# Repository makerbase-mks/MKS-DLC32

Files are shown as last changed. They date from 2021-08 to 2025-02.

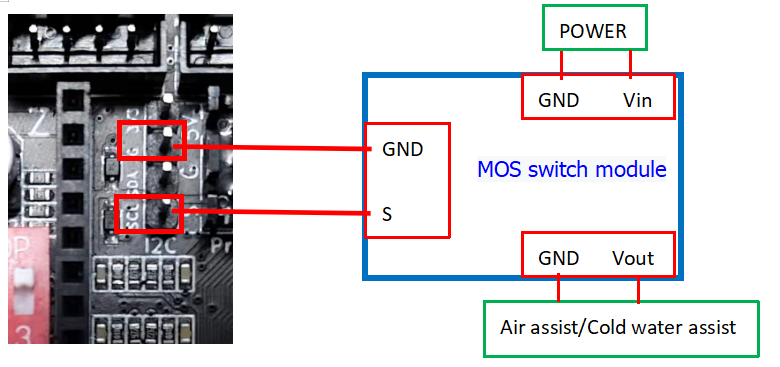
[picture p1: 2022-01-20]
MKS-DLC32-main/images/Hardware Wiring1.png

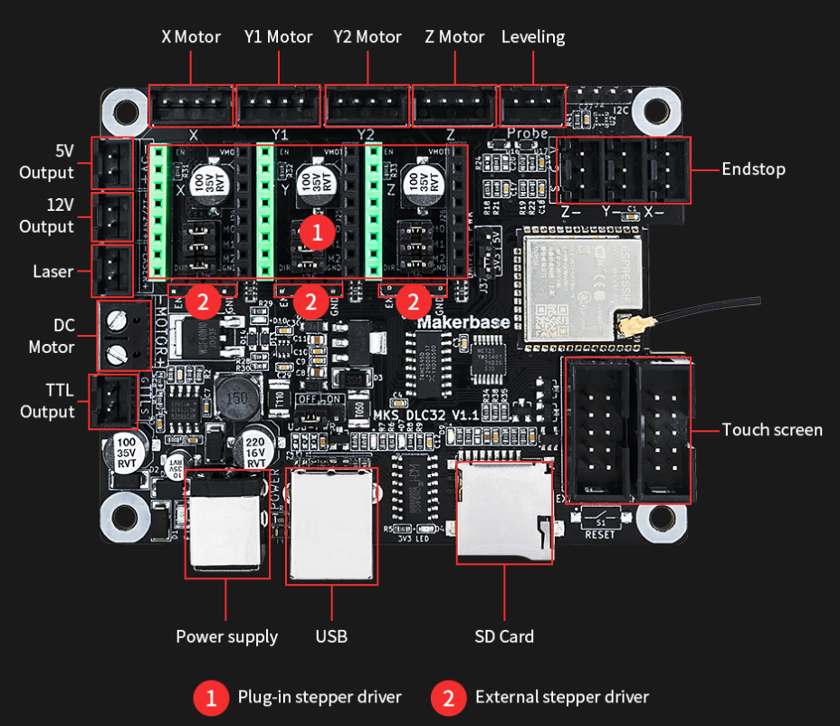
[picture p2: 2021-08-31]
MKS-DLC32-main/images/interface.png

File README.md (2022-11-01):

# MKS-DLC32
MKS DLC32 motherboard kit, which is an offline engraving master control kit developed for desktop engraving machines. The hardware is equipped with a 32-bit high-speed ESP32 module, integrated WIFI function, and directly drives a 3.5-inch touch color screen; it can realize fast engraving and WEB web pages. Control, mobile phone APP control and other functions.  
The mounting holes and board size of MKS DLC32 are compatible with MKS DLC, and the it can also be used with the [LaserGRBL](https://lasergrbl.com) and [LightBurn](https://lightburnsoftware.com) PC software.  
main   

## Related tutorials and Notice
Product introduce video: https://www.youtube.com/watch?v=U_OzlMxwms8&t=6s  
Basic usage for laser engraving machine: https://www.youtube.com/watch?v=MKRBYVbxJmw&t=139s  

# HARDWARE Wiring 
For detailed wiring method, please refer to: https://github.com/makerbase-mks/MKS-DLC32/blob/main/doc/DLC32%20wiring%20manual.pdf

# Compare between MKS DLC and MKS DLC32
| ITEMS | MKS DLC | MKS DLC32 |
| --- | --- | --- |
| MCU | ATMEGA328P ( 8bits) | ESP32-WROOM-32U（ 32bits）  |
| MCU Freq. | 20MHz | 240MHz |
| FLASH | 32KBytes | 8192KBytes |
| RAM | 32KBytes | 520KBytes |
| Power Input | DC 12v/24v | DC12v/24v |
| Laser Speed | <=3000mm/min | <=8000mm/min |
| PC engraving | Support | Support |
| Offline Mode | Not Support | Support |
| LCD | Not Support | Support，3.5 inch Touch TFT |
| WiFi On Board | Not Support | Support |
| Web Control | Not Support | Support |
| Mobile APP Control | Not Support | Support |
| LaserGRBL | Support | Support |
| LightBurn | Support | Support |

# FIRMWARE
Refer to the wiki:https://github.com/makerbase-mks/MKS-DLC32/wiki/Firmware  
Source: https://github.com/makerbase-mks/MKS-DLC32-FIRMWARE  

# Mobile App
Refer to the wiki:https://github.com/makerbase-mks/MKS-DLC32/wiki/Mobile-App

# Wiki
https://github.com/makerbase-mks/MKS-DLC32/wiki

# Purchase link
Aliexpress: https://www.aliexpress.com/item/1005003183498253.html?spm=a2g0o.store_pc_home.productList_8356958.pic_0

## Note
- Thank you for using MKS products. If you have any questions during use, please contact us in time and we will work with you to solve it.
- For more product dynamic information and tutorial materials, you can always follow MKS's Facebook/Twitter/Discord/Reddit/Youtube and Github. Thank you!
- MKS Github: https://github.com/makerbase-mks  
- MKS Facebook: https://www.facebook.com/Makerbase.mks/  
- MKS Twitter: https://twitter.com/home?lang=en  
- MKS Discord: https://discord.gg/4uar57NEyU
- MKS Reddit: https://www.reddit.com/user/MAKERBASE-TEAM/ 

mks_link

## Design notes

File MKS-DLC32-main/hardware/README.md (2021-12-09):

# MKS-DLC32 Hardware
- V2.1_003
  - MKS DLC32 V2.1_003 TOP.pdf
  - MKS DLC32 V2.1_003 BOTTOM.pdf
  - MKS DLC32 V2.1_003 PIN.pdf
  - MKS DLC32 V2.1_003 SCH.pdf
  - MKS DLC32 V2.1_003 SIZE.pdf
  
  change log
  - From V2.1_002 version
    - Add the driver slot silk screen, and the endstops silk screen is on the motherboard BOTTOM
	- V2.1_002 change to V2.1_003

- V2.1_002
  - MKS DLC32 V2.1_002 TOP.pdf
  - MKS DLC32 V2.1_002 BOTTOM.pdf
  - MKS DLC32 V2.1_002 PIN.pdf
  - MKS DLC32 V2.1_002 SCH.pdf
  - MKS DLC32 V2.1_002 SIZE.pdf
  
  change log
  - From V2.1_001 version
    - The direction of J18 buckle is 180 degrees, the line sequence remains unchanged 
	- V2.1_001 change to V2.1_002
  
- V2.1_001
  - MKS DLC32 V2.1_001 TOP.pdf
  - MKS DLC32 V2.1_001 BOTTOM.pdf
  - MKS DLC32 V2.1_001 PIN.pdf
  - MKS DLC32 V2.1_001 SCH.pdf
  - MKS DLC32 V2.1_001 SIZE.pdf
  
  change log
  - From V2.0_001 version
    - Mounting hole adjustment 
	- PCB is black immersion gold 
	- V2.0_001 change to V2.1_001

- V2.0_001
  - MKS DLC32 V2.0_001 TOP.pdf
  - MKS DLC32 V2.0_001 BOTTOM.pdf
  - MKS DLC32 V2.0_001 PIN.pdf
  - MKS DLC32 V2.0_001 SCH.pdf
  - MKS DLC32 V2.0_001 SIZE.pdf
  
  change log
  - From V1.1_002 version
    - Add power switch package(NC)
	- Fuse use plug-in type
	- Add debug led for wifi
	- Reset botton use XH2.54-2P
    - Optimize the laser and spindle circuit (Increase diode)
	- Add beerper interface XH2.54-2P
	- Optimize the driver circuit (add 6.8k for driver output)
	- Relayout and change board outline
	- Some io function adjustments (IO32 for TTL, IO22 for Probe, IO2 for wifi debug led)
	- Microstep settings using DIP switch 
	- V1.1_002 change to V2.0_001

- V1.1_002
  - MKS DLC32 V1.1_002 TOP.pdf
  - MKS DLC32 V1.1_002 BOTTOM.pdf
  - MKS DLC32 V1.1_002 PIN.pdf
  - MKS DLC32 V1.1_002 SCH.pdf
  - MKS DLC32 V1.1_002 SIZE.pdf
  
  change log
  - From V1.1_001 version
    - Optimize the laser circuit 
	- 001 change to 002

- V1.1_001
  - MKS DLC32 V1.1_001 TOP.pdf
  - MKS DLC32 V1.1_001 BOTTOM.pdf
  - MKS DLC32 V1.1_001 PIN.pdf
  - MKS DLC32 V1.1_001 SCH.pdf
  - MKS DLC32 V1.1_001 SIZE.pdf

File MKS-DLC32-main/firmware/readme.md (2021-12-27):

## List of upload Firmware
There are several compiled firmwares that can be downloaded here:  
[For Laser, normal machine](https://github.com/makerbase-mks/MKS-DLC32/tree/main/firmware/Laser/Normal)  
[For Laser, CoreXY machine](https://github.com/makerbase-mks/MKS-DLC32/tree/main/firmware/Laser/CoreXY)  
[For CNC, normal machine](https://github.com/makerbase-mks/MKS-DLC32/tree/main/firmware/CNC/Normal)(For beta)  
The firmware of MKS DLC32 has been burned with laser normal machine before leaving the factory. 

## Method of upload Firmware

You can either use the "MKS ESP32 Download Tool" or "Flash Download Tools" upload firmware of MKS DLC32.
### MKS ESP32 Download Tool
MKS ESP32 Download Tool is specially developed by MKS to simplify the uploading operation. It is recommended to use. For detailed usage, please refer to:https://github.com/makerbase-mks/MKS-DLC32/blob/main/doc/DLC32%20Firmware%20Programming%20Instructions.pdf

### Flash Download Tools
#### Windows

1. On Windows PC, download the "Flash Download Tools" from https://www.espressif.com/en/support/download/other-tools 
2. Open the "Flash Download Tools", choose "Developer Mode"->ESP32 DowloadTool, and it will open the main menu.
3. Config the Flash Download Tools  
3.1 Choose the firmware(binary file listed above) and fill the address to be 0  
3.2 Config the  spiFlash  
SPI speed: 40MHz  
SPI MODE: DOUT  
Flash Size: 32Mbit  
3.3 Connect MKS DLC32 to PC using the USB line. Choose the COM of the DLC32, if you can’t find the COM, please check if the CH340 driver has been installed on the PC.  
3.4 Choose the baudrate which can be over 115200(The greater the baud rate, the faster the transmission speed, but the greater the chance of transmission errors).  
3.5 Press START and it will start to upload, just wait it to be finished.

微信图片_20210908150315

#### Linux

* Install esptool.py
```
pip install esptool
```

* Provide valid path to port/firmware and burn the ESP32 chip
```
esptool.py --baud 300000 --chip esp32 --port /dev/ttyUSB0 write_flash --flash_mode dio --flash_size detect 0x0 TS35/Laser/Normal/Board_V2.0/V2.0.4_H35_20211123_N.bin
```

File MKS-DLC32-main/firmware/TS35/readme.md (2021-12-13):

# Version description

## E.g：

### V2.0.4_H35_20211108_N

V2.0.4.: Firmware version

H35: Horizontal screen- 3.5Inch

20211108： Modified date （2021-11-08）

N：N for normal machine, C for CoreXY machine

(for DLC V2.x, coreXY): As there is a little difference between DLC V1.x and V2.x boards, so we would explain what board the firmware is suitable for. 
**Please use the correct version, otherwise it may not work.**

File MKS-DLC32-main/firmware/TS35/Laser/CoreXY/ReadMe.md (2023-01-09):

# Update:
## Version description

E.g：

### V2.0.3_H35_20211108_N

V2.0.3.: Firmware version

H35: Horizontal screen- 3.5Inch

20211108： Modified date （2021-11-08）

N：N for normal machine, C for CoreXY machine

(for DLC V2.x, coreXY): As there is a little difference between DLC V1.x and V2.x boards, so we would explain what board the firmware is suitable for. Please use the correct version, otherwise it may not work.

### 2022-12-23

##### Update version: V2.30_H35_2022_1223_C_ZX_001

- Fixed incompatibility between UI buttons and background
- Fixed an issue where WiFi could not be found
- Temporarily cancel automatic WiFi reconnection
- Fixed some other known bugs

### 2022-07-04

##### Update version: V2.10_H35_2022_0704_C_ZX_001

- Add z-axis control on the screen
- Add German, Spanish and Portuguese
- Add a cooling button
- Add the symbol "_" to the keyboard
- Fix some known bugs

## Update:

### 2022-01-05

##### Update version: V2.0.8_H35_20220105_C

- Fixed the problem of "warning text" displayed abnormally in the pop-up window after clicking the positioning during the moving process
- In the Chinese environment, the display of "Continue/Cancel" in the pop-up window of more than 1M side patrol is missing
- Unable to flash configuration file
- Inaccurate screen edge size

### 2021-12-22

##### Update version: V2.0.8_H35_20211222_C

- Fix part of the error display
- Fix language errors
- Optimize wifi function
- WebUI updated

### 2021-12-13

##### Update version: V2.0.7_H35_20211213_C

- Fix language display error
- Join the function of MIST, you can use M7/M9 to control，Connect the control signal pin to the SCL pin of I2C. The control level of SCL is only 0-3.3V, so an external level conversion module is required for control

### 2021-12-07

##### Update version: V2.0.6_H35_20211207_C

- Fix the version number error displayed on Lightburn

### 2021-11-23

**Update version: V2.0.4_H35_20211123_C**

Fix content

- Optimize the time to automatically connect to the wifi  
- Fix the problem that it cannot be moved when $1=255  
- Modify the language switch interface  
- Fixed the problem of searching blank lists when searching on wifi  
- Fixed the problem that the options on the power adjustment interface did not change after triggering the laser automatic protection, and the problem that the value on the main page did not change  
- Fix some pop-up errors

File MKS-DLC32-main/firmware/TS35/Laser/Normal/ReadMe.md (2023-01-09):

# Update:
## Version description

E.g：

### V2.0.3_H35_20211108_N

V2.0.3: Firmware version

H35: Horizontal screen- 3.5Inch

20211108： Modified date （2021-11-08）

N：N for normal machine, C for CoreXY machine

(for DLC V2.x, coreXY): As there is a little difference between DLC V1.x and V2.x boards, so we would explain what board the firmware is suitable for. Please use the correct version, otherwise it may not work.

## Update:

### 2022-12-23

##### Update version: V2.30_H35_2022_1223_N_ZX_001

- Fixed incompatibility between UI buttons and background
- Fixed an issue where WiFi could not be found
- Temporarily cancel automatic WiFi reconnection
- Fixed some other known bugs

### 2022-11-04

##### Update version: V2.20_H35_2022_1101_N_ZX_002

- Change the UI
- Optimize file transfer
- Added WiFi mode switching through the screen
- Fix some known bugs

### 2022-06-29

##### Update version: V2.10_H35_2022_0621_N_ZX_001

- Add z-axis control on the screen
- Add German, Spanish and Portuguese
- Add a cooling button
- Add the symbol "_" to the keyboard
- Fix some known bugs

### 2022-01-05

##### Update version: V2.0.8_H35_20220105_N

- Fixed the problem of "warning text" displayed abnormally in the pop-up window after clicking the positioning during the moving process
- In the Chinese environment, the display of "Continue/Cancel" in the pop-up window of more than 1M side patrol is missing
- Unable to flash configuration file
- Inaccurate screen edge size

### 2021-12-22

##### Update version: V2.0.8_H35_20211222_N

- Fix part of the error display
- Fix language errors
- Optimize wifi function
- WebUI updated

### 2021-12-13

**Update version: V2.0.7_H35_20211213_N**

- Fix language display error
- Join the function of MIST, you can use M7/M9 to control，Connect the control signal pin to the SCL pin of I2C. The control level of SCL is only 0-3.3V, so an external level conversion module is required for control

### 2021-12-07

**Update version: V2.0.6_H35_20211207_N**

- Fix the version number error displayed on Lightburn

### 2021-11-23

**Update version: V2.0.4_H35_20211123_N**

Fix content

- Optimize the time to automatically connect to the wifi  
- Fix the problem that it cannot be moved when $1=255  
- Modify the language switch interface  
- Fixed the problem of searching blank lists when searching on wifi  
- Fixed the problem that the options on the power adjustment interface did not change after triggering the laser automatic protection, and the problem that the value on the main page did not change  
- Fix some pop-up errors

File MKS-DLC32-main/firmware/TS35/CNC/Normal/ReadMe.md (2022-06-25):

# Update:
### 2022-06-25

##### Update version: V2.1.0_H35_20220526_02_N_CNC

- Add the thickness setting of the short-circuit block (set the value of $46)
- Add hard reset button and sound control switch button on the screen
- Add symbol "_" to keyboard
- Fix some known bugs

### 2022-05-11

##### Update version: V2.1.0_H35_20220510_N_CNC_001

- Add on-screen knife buttons
- Add button sound and Chinese environment
- Disable the automatic return to zero after the engraving is complete
- Adjust the WEB interface
- Fix some known bugs

### 2022-01-05

##### Update version: V2.0.8_H35_20211222_N_CNC

- Fix the problem that the configuration file cannot be recognized
- Fix the WiFi name is not displayed after automatically connecting to WiFi
- Cancel M7, retain M8, release Z limit function, you can configure whether Z return to zero is required through instructions

### 2021-12-22

##### Update version: V2.0.8_H35_20211222_N_CNC

- Fix part of the error display
- Fix language errors
- Optimize wifi function
- WebUI updated
- Fix the problem of returning to zero error

## 2021.12.13

##### Update version: V2.0.7_H35_20211213_N_CNC

- Fixed incorrect display of some languages
- Add FlOOD control function, use M8 control, M9 disable，Connect the control signal pin to the SCL pin of I2C. The control level of SCL is only 0-3.3V, so an external level conversion module is required for control

## 2021.12.07

##### Update version: V2.0.6_H35_20211207_N_CNC

- Fixed the incorrect version number displayed when using Lightburn
- Repair abnormal speed during engraving
- Join wifi automatic connection
- Add the function of Probe, you can use external probe

## 2021.12.06

**Update version: V2.0.4_H35_20211206_N_CNC.bin**

 - Repair the power display is not correct after returning to zero
 - Join wifi to automatically reconnect
 - Fix the problem of garbled characters in the card reader

## 2021.11.23
**Update version: V1.21_H35_20211009_N_CNC.bin**

 - Fix the problem that $1=255 cannot be locked 
 - Fix the problem that after some pop-up windows appear, they can't pop up in the follow-up 
 - Fix the problem of Z zero return error 
 - Fix the problem that the default value is not restored when re-sculpting after adjusting FeedOverride/SpindleSpeedOverride during engraving

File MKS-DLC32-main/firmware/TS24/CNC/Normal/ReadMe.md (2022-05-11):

# Update:
## Version description

E.g：

### V2.0.3_H35_20211108_N

V2.0.3: Firmware version

H35: Horizontal screen- 3.5Inch

20211108： Modified date （2021-11-08）

N：N for normal machine, C for CoreXY machine

(for DLC V2.x, coreXY): As there is a little difference between DLC V1.x and V2.x boards, so we would explain what board the firmware is suitable for. Please use the correct version, otherwise it may not work.

## Update:

### 2022-05-11

##### Update version: V2.1.0_H24_20220511_01_N_CNC

- Add on-screen knife buttons
- Add button sound and Chinese environment
- Disable the automatic return to zero after the engraving is complete
- Adjust the WEB interface
- Fix some known bugs

### 2022-01-08

**Update version: V2.0.8_H24_20220108_N_CNC**

- Change the direction of the Y-axis of the control interface to make it consistent with the direction of LASERGRBL
- On the keyboard, use "AB" and "ab" to replace spaces when switching between uppercase and lowercase

### 2021-12-23

**Update version: V2.0.8_H24_20211223_N_CNC**

- Fix some language description errors
- Adjust the position of the X and Y icons
- Fix the problem of incorrect display of the version number on the web

### 2021-12-22

**Update version: V2.0.8_H24_20211222_N_CNC**

- Fix language errors
- Update webUI
- Fix the problem that Probe does not work
- Optimize wifi function

### 2021-12-14

**Update version: V2.0.7_H24_20211214_N_CNC**

- Fix language display error
- Add FlOOD control function, use M8 control, M9 disable，Connect the control signal pin to the SCL pin of I2C. The control level of SCL is only 0-3.3V, so an external level conversion module is required for control
- Add the function of Probe, you can use external probe

### 2021-12-09

**Update version: V2.0.6_H24_20211209_N_CNC**

- Fix the version number error displayed on Lightburn

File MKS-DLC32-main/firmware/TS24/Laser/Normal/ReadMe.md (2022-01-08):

# Update:
## Version description

E.g：

### V2.0.3_H35_20211108_N

V2.0.3: Firmware version

H35: Horizontal screen- 3.5Inch

20211108： Modified date （2021-11-08）

N：N for normal machine, C for CoreXY machine

(for DLC V2.x, coreXY): As there is a little difference between DLC V1.x and V2.x boards, so we would explain what board the firmware is suitable for. Please use the correct version, otherwise it may not work.

## Update:

### 2022-01-08

**Update version: V2.0.8_H24_20220107_N**

- Change the direction of the Y-axis of the control interface to make it consistent with the direction of LASERGRBL
- On the keyboard, use "AB" and "ab" to replace spaces when switching between uppercase and lowercase

### 2021-12-23

**Update version: V2.0.8_H24_20211223_N**

- Adjust X, Y icon position

### 2021-12-22

**Update version: V2.0.8_H24_20211222_N**

- Fix language errors
- Update webUI
- Optimize wifi function

### 2021-12-14

**Update version: V2.0.7_H24_20211214_N**

- Fix language display error
- Join the function of MISP, you can use M7/M9 to control，Connect the control signal pin to the SCL pin of I2C. The control level of SCL is only 0-3.3V, so an external level conversion module is required for control

### 2021-12-09

**Update version: V2.0.6_H24_20211209_N**

- Fix the version number error displayed on Lightburn

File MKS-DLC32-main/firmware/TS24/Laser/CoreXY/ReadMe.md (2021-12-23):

# Update:
## Version description

E.g：

### V2.0.3_H35_20211108_N

V2.0.3: Firmware version

H35: Horizontal screen- 3.5Inch

20211108： Modified date （2021-11-08）

N：N for normal machine, C for CoreXY machine

(for DLC V2.x, coreXY): As there is a little difference between DLC V1.x and V2.x boards, so we would explain what board the firmware is suitable for. Please use the correct version, otherwise it may not work.

## Update:

### 2021-12-23

**Update version: V2.0.8_H24_20211223_C**

- Adjust X, Y icon position

**Update version: V2.0.8_H24_20211222_C**

- Fix language errors
- Update webUI
- Optimize wifi function

### 2021-12-14

**Update version: V2.0.7_H24_20211214_C**

- Fix language display error
- Join the function of MISP, you can use M7/M9 to control，Connect the control signal pin to the SCL pin of I2C. The control level of SCL is only 0-3.3V, so an external level conversion module is required for control

### 2021-12-09

**Update version: V2.0.6_H24_20211209_C**

- Fix the version number error displayed on Lightburn

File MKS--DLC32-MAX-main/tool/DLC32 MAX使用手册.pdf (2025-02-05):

# MKS DLC32 MAX 主板使用说明

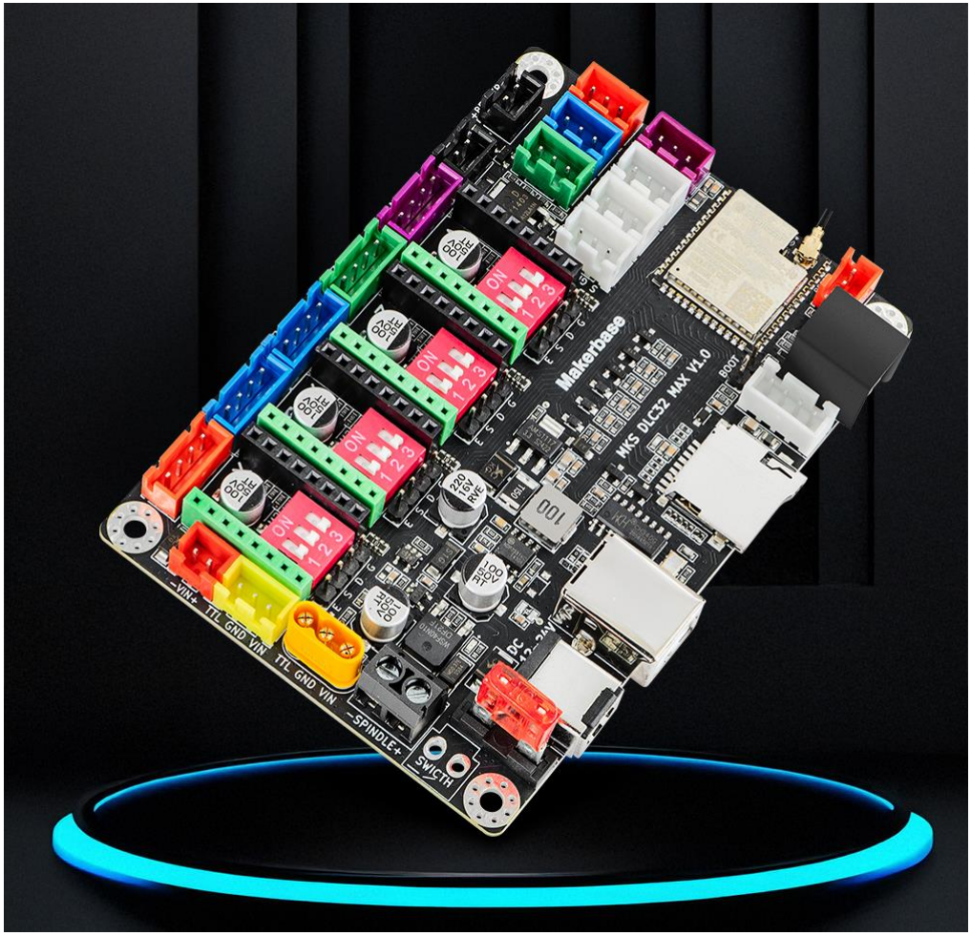
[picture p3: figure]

简介

MKS DLC32 MAX 激光雕刻控制板由创客基地(Makerbase)倾力打造,是一款集高性能强扩展性与智能操

控于一体的雕刻控制解决方案。搭载 ESP32-S3 系列芯片，同时支持 CNC 与激光雕刻，可支持 CNC 的 A

轴，激光雕刻机最大可达 60W 激光头雕刻功率与 30000mm/min 速度，满足高效创作。

可以兼容插拔式驱动扩展性强，如可接 TMC2209 超静音驱动方案和 TB67S109 大电流驱动模块，另外

还可以连接外部驱动。

安全方面，可以配备开盖保护、火焰检测等智能安全功能，为用户创作保驾护航。

可以无需长时间连接电脑,支持手机 APP 与 Web 局域网远程控制,让操作更加自由便捷,不论是激光雕

刻还是 CNC 应用，MKS DLC32 MAX 都是解锁创意无限的理想选择!

本文档可作为初次使用 MKS DLC32 主板参考，文档将会从以下几部分进行说明：

固件的下载与更新，硬件连接说明，Wifi 连接说明及远程控制说明，主板参数设置

，主板常见问题及其解决办法。

目录

一． 固件的下载与更新---------------------------------------------------------------------------------------------------------------------4

1. 固件与烧录软件的下载 -------------------------------------------------------------------------------------------------------------4

1.1 固件的选择与下载 -------------------------------------------------------------------------------------------------------------4

1.2 烧录软件与 USB 驱动软件安装---------------------------------------------------------------------------------------------4

2. 烧录软件的安装于说明与固件烧录 ---------------------------------------------------------------------------------------------5

2.1 软件安装与连接-----------------------------------------------------------------------------------------------------------------5

2.2 软件介绍与固件烧录----------------------------------------------------------------------------------------------------------7

二． 主板硬件连接及接口说明-----------------------------------------------------------------------------------------------------------9

1. 主板接口图及安装尺寸-------------------------------------------------------------------------------------------------------------9
2. DLC32 主板接口说明---------------------------------------------------------------------------------------------------------------- 10

2.1 电源输入部分------------------------------------------------------------------------------------------------------------------ 10

2.2 电机驱动部分------------------------------------------------------------------------------------------------------------------ 11

2.3 激光头接法--------------------------------------------------------------------------------------------------------------------- 13

2.4 CNC 主轴接法------------------------------------------------------------------------------------------------------------------ 15

2.5 限位开关------------------------------------------------------------------------------------------------------------------------ 16

2.6 PROBE（对刀）、安全接口------------------------------------------------------------------------------------------------- 17

2.8 蜂鸣器、空气辅助接口---------------------------------------------------------------------------------------------------- 17

2.9 急停开关接口：--------------------------------------------------------------------------------------------------------------- 18

2.10 屏幕、手柄接口------------------------------------------------------------------------------------------------------------- 18

2.11 TF 卡、PC 接口 --------------------------------------------------------------------------------------------------------------- 19

三 . 主板参数设置-------------------------------------------------------------------------------------------------------------------------- 19

四．常见支持指令--------------------------------------------------------------------------------------------------------------------------- 22

五．常见报错说明--------------------------------------------------------------------------------------------------------------------------- 23

六．主板常见问题及其解决办法 ------------------------------------------------------------------------------------------------------- 24

七 . 技术支持及保证----------------------------------------------------------------------------------------------------------------------- 25

## 一． 固件的下载与更新

操作流程如下：

- 固件与烧录软件的下载
- 烧录软件的安装于说明与固件烧录

### 1. 固件与烧录软件的下载

MKS 官方的 Github 进行下载：https://github.com/makerbase-mks/MKS-DLC32

### 1.1 固件的选择与下载

打开以上链接后，选择“MKS--DLC32-MAX-main”这栏打开，然后下里面的固件即可，如下图所示：

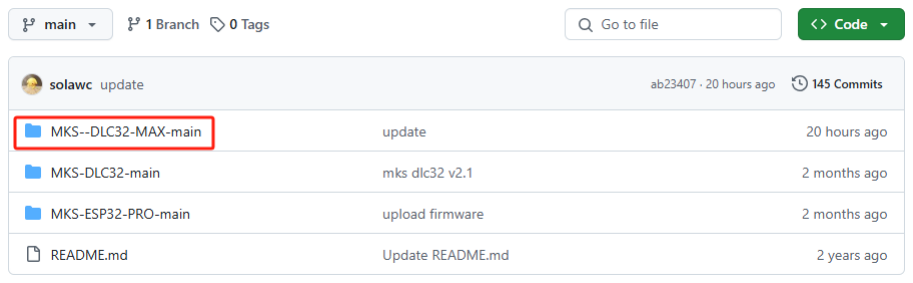
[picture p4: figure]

### 1.2 烧录软件与 USB 驱动软件安装

下载链接

https://github.com/makerbase-mks/MKS-DLC32/tree/main/MKS--DLC32-MAX-main/tool

MKS LaerTool 烧录软件和 CH340 驱动安装文件下载页面最新版本即可。

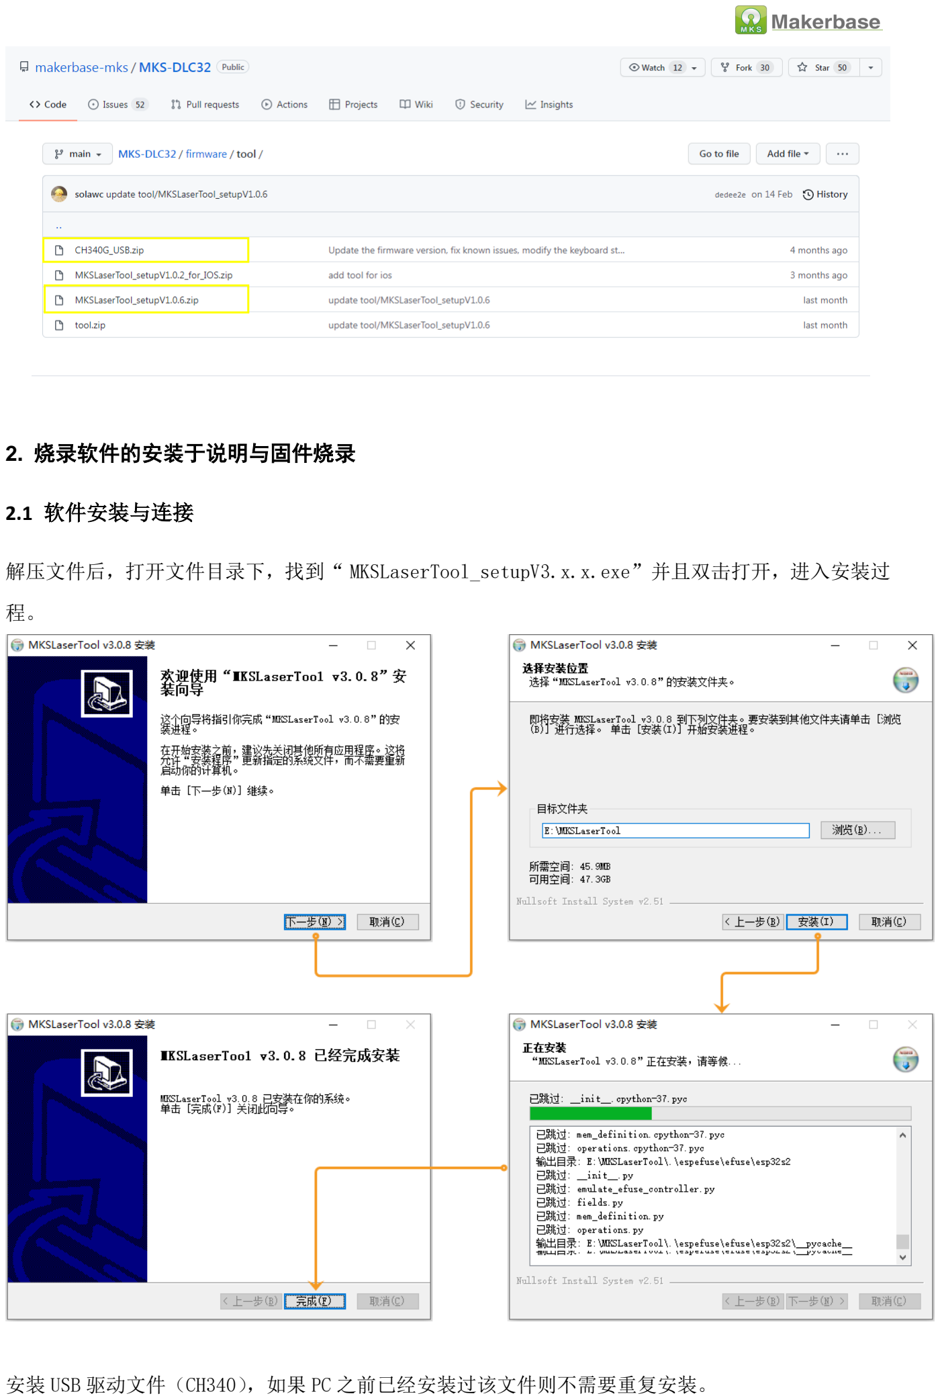
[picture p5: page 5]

### 2. 烧录软件的安装于说明与固件烧录

### 2.1 软件安装与连接

解压文件后，打开文件目录下，找到“ MKSLaserTool_setupV3.x.x.exe”并且双击打开，进入安装过

程。

安装 USB 驱动文件（CH340），如果 PC 之前已经安装过该文件则不需要重复安装。

安装完成之后，可将 MKS DLC32 主板通过 USB 线连接至 PC，在 PC 设备管理中，查看主板是否有被分

配相应的 COM。正常分配则主板已连接上 PC,如果没有显示的话，请重新检查软件的安装，和硬件的连

接是否存在问题。

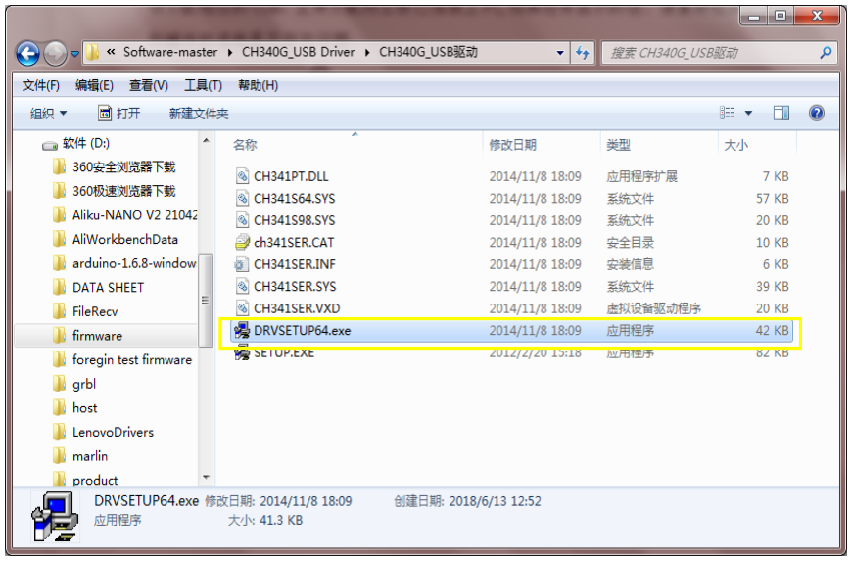
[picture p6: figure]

主板在连接 USB 到 PC 时，同时需要连接 12-24v 进行供电，如果未连接 12-24v 供电，主板将无法别识

别。

如下图，为连接后，com 正确识别。

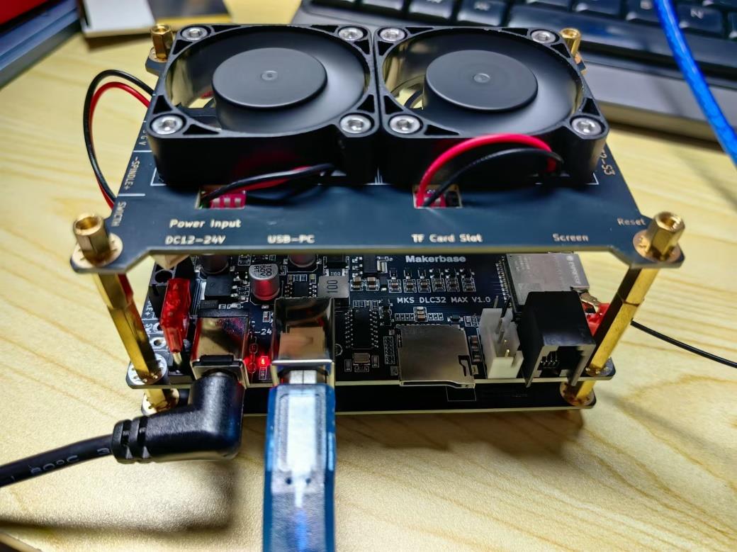
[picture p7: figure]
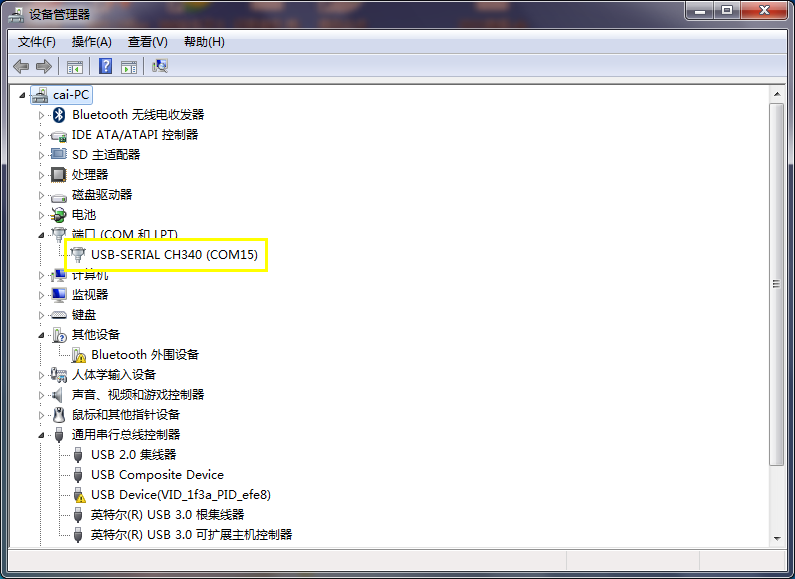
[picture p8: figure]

### 2.2 软件介绍与固件烧录

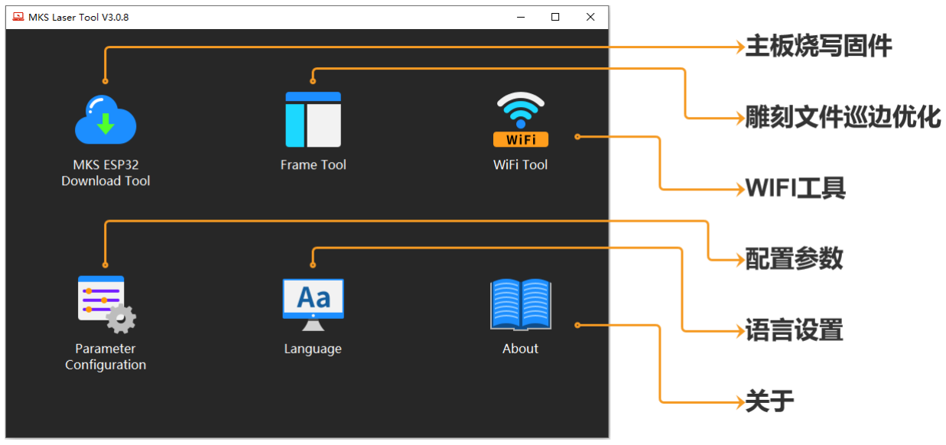
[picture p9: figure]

点击“MKS ESP32 Download Tool”，进入烧写界面

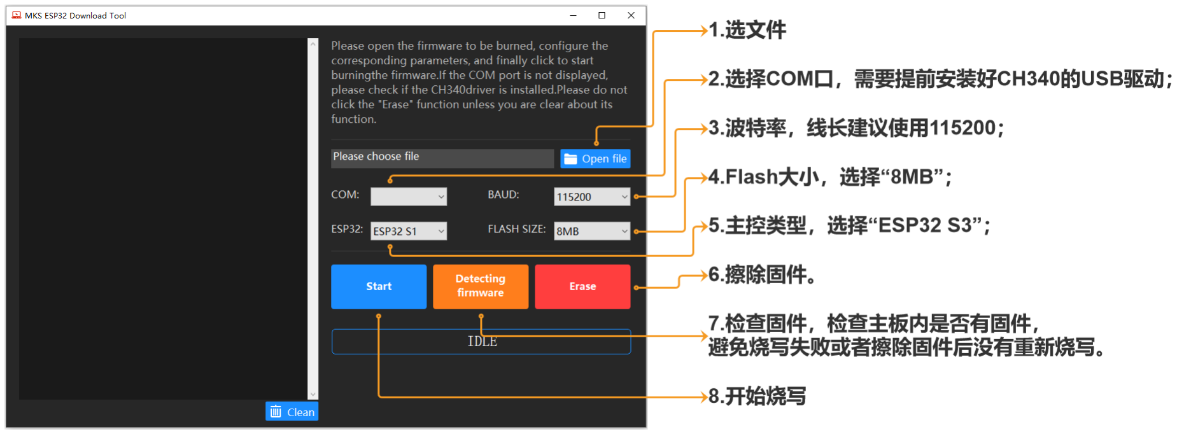
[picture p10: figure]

烧录文件为从 github 下载，符合机器情况的 bin 文件。

COM:可在设备管理器中，查看到具体的 COM 序号，按照实际情况进行设置。

BAUD：波特率一般建议选择 115200。

Flash 大小：这个需要选择 8MB 的。

主控类型：选择 ESP32 S3。

烧写步骤：点击烧写按键。如果出现烧写失败时，先点击擦除，然后再点击烧写，并且将波特率数值

降低。

完成设置之后，点击开始，等待烧录完成即可。

## 二． 主板硬件连接及接口说明

1. 主板接口图及安装尺寸

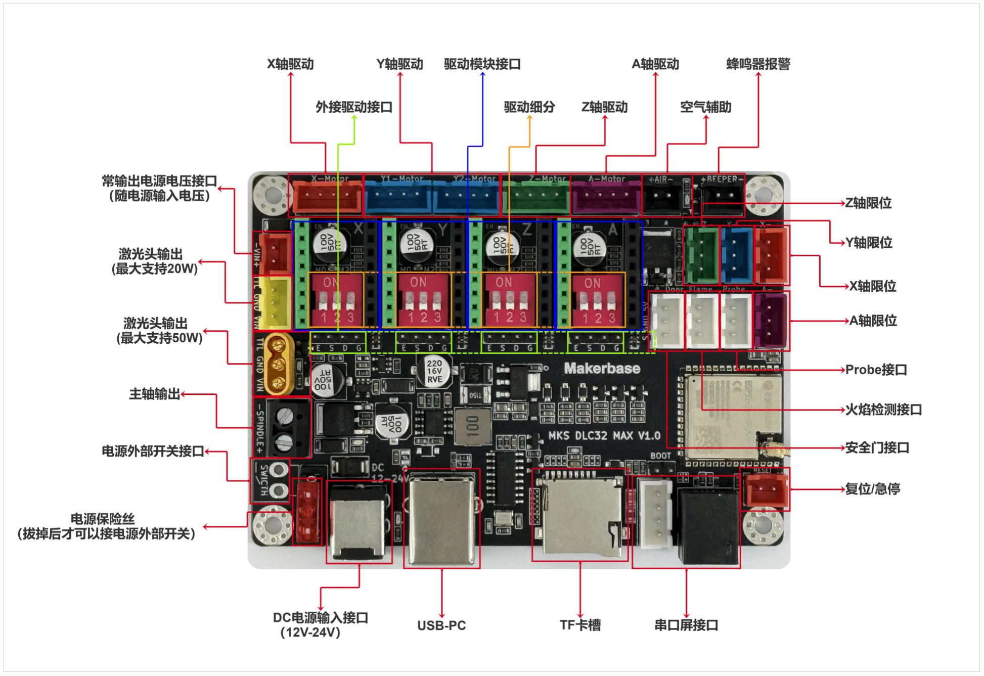
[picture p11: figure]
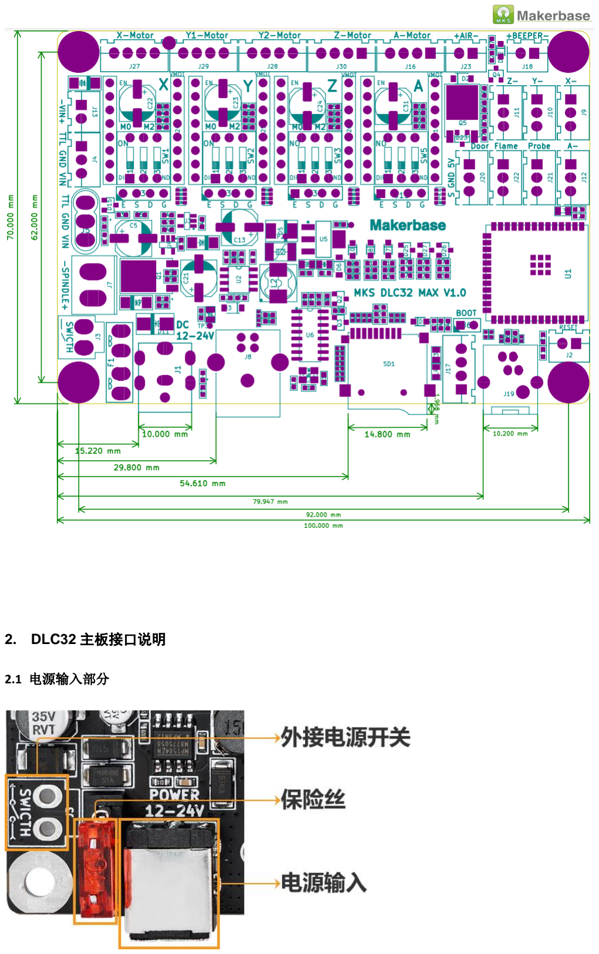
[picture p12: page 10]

### 2. DLC32 主板接口说明

### 2.1 电源输入部分

电源输入：该接口可接 12V 或者 24V 电源，最大承受电流 5A，电源输入端子为“DC-007B-2.1mm”接

口。

保险丝：10A 保险丝，如需外接开关控制电源，需要拔掉保险丝才可以。

外接电源开关：可以用来外接开关来控制电源，但需要拔掉保险丝。注意：这个接口不是电源输入接

口，切记不能接电源。

### 2.2 电机驱动部分

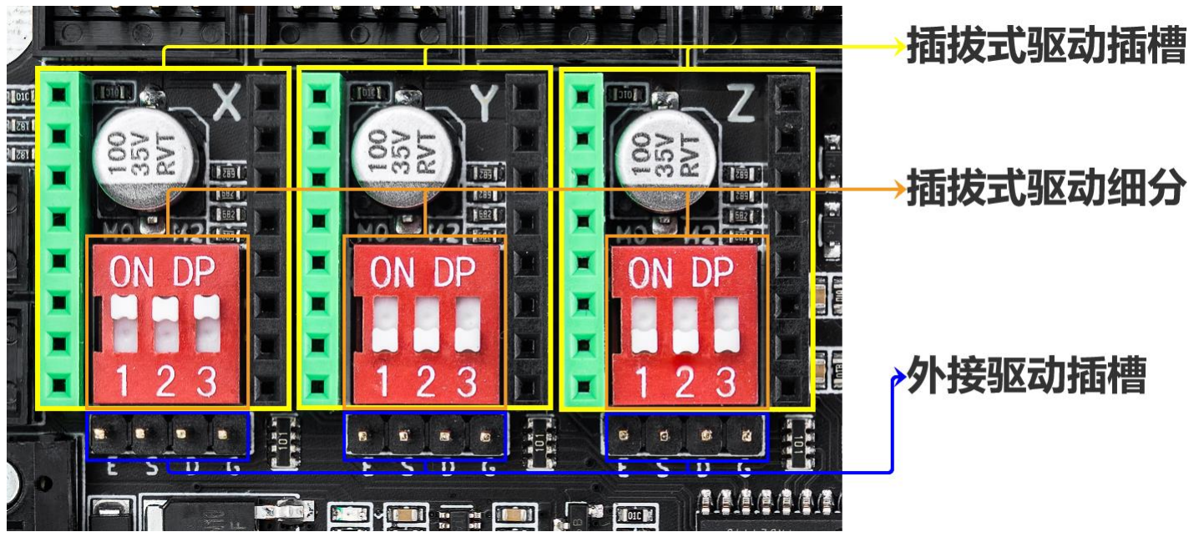
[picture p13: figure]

2.2.1 接口示意图

插拔式驱动插槽 PIN | 插拔式驱动细分设置开关

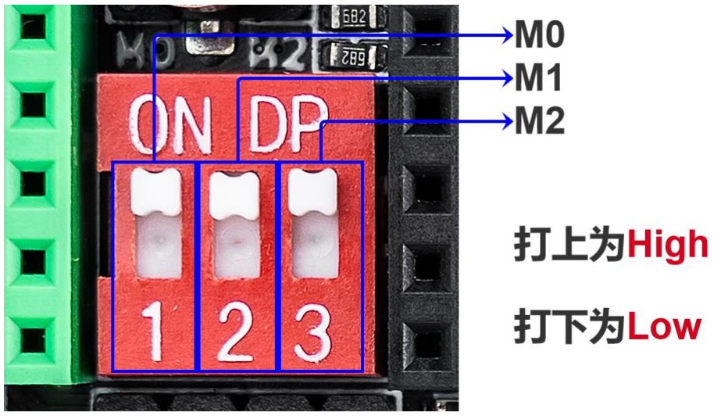
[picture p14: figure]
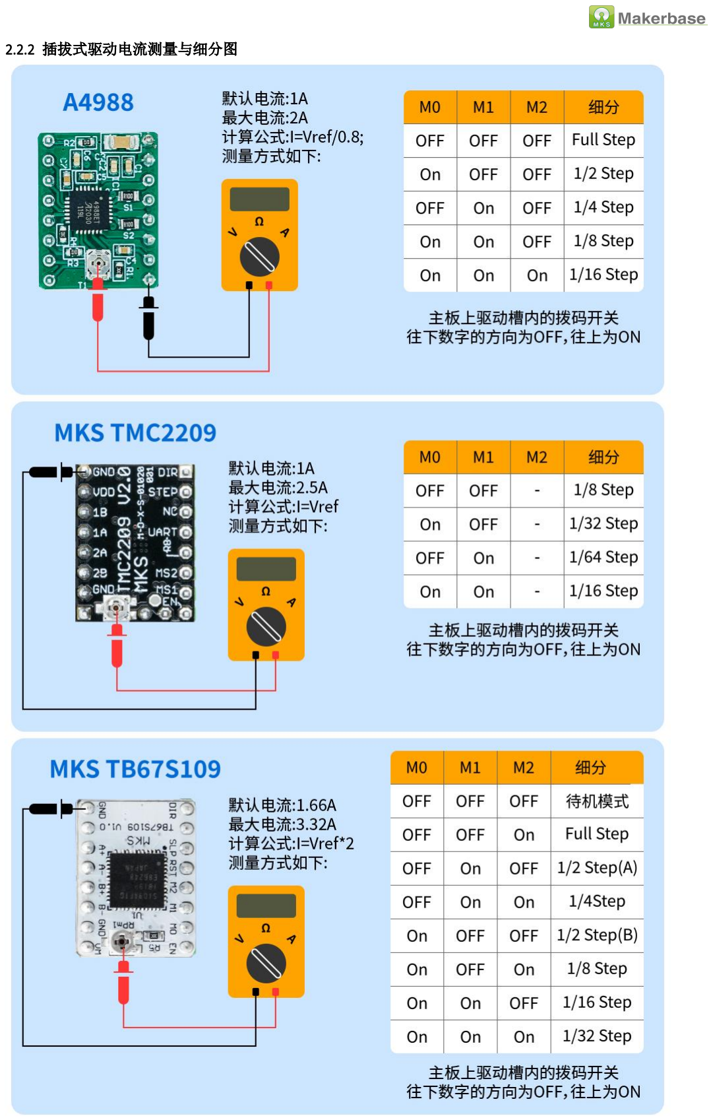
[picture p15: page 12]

2.2.2 插拔式驱动电流测量与细分图

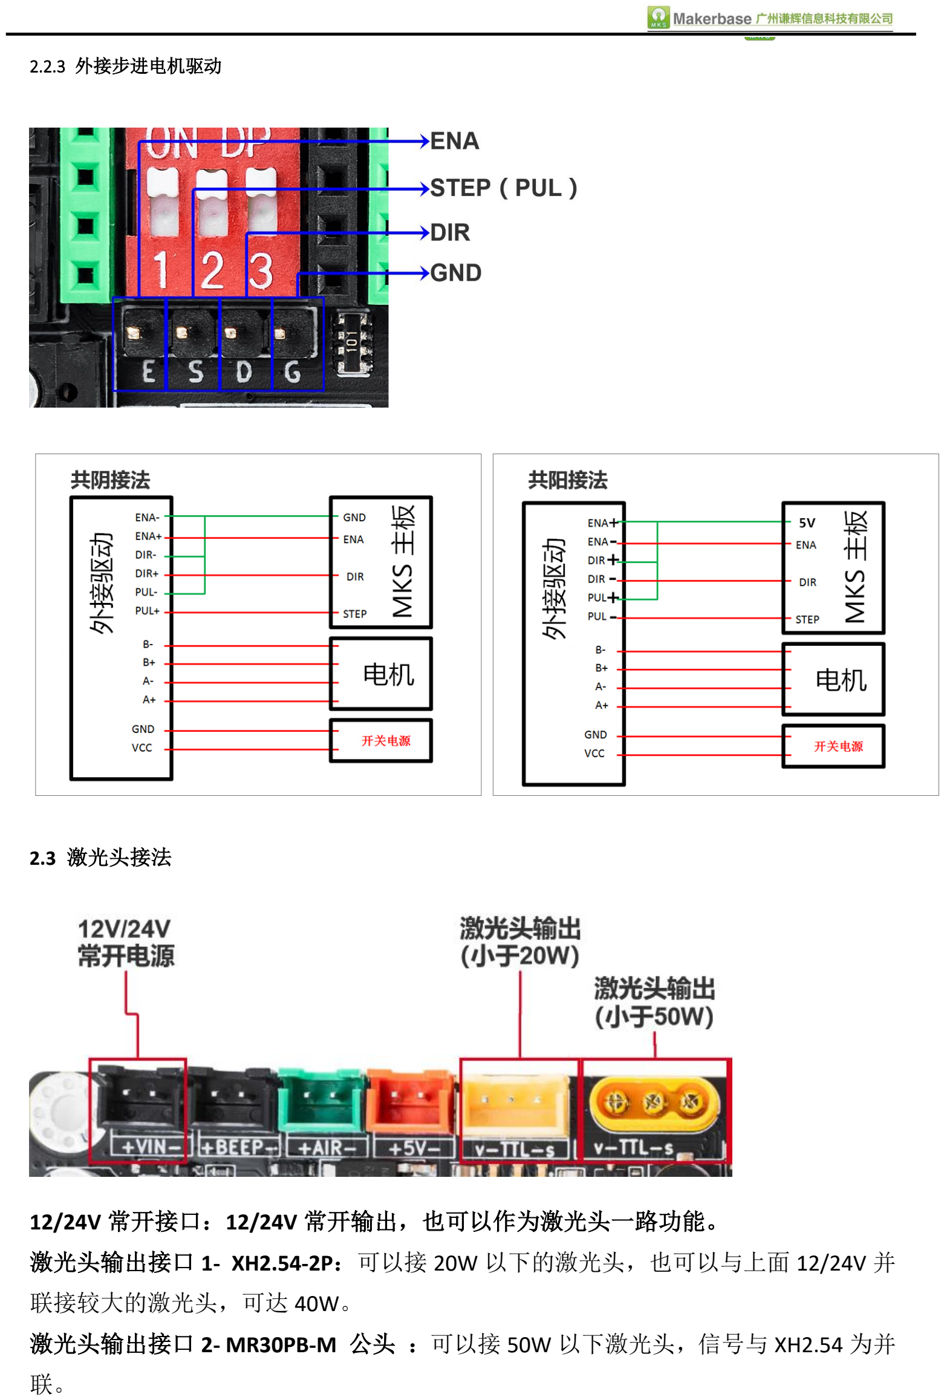
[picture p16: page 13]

2.2.3 外接步进电机驱动

### 2.3 激光头接法

### 12/24V 常开接口：12/24V 常开输出，也可以作为激光头一路功能。

### 激光头输出接口 1- XH2.54-2P：可以接 20W 以下的激光头，也可以与上面 12/24V 并

### 联接较大的激光头，可达 40W。

### 激光头输出接口 2- MR30PB-M 公头 ：可以接 50W 以下激光头，信号与 XH2.54 为并

联。

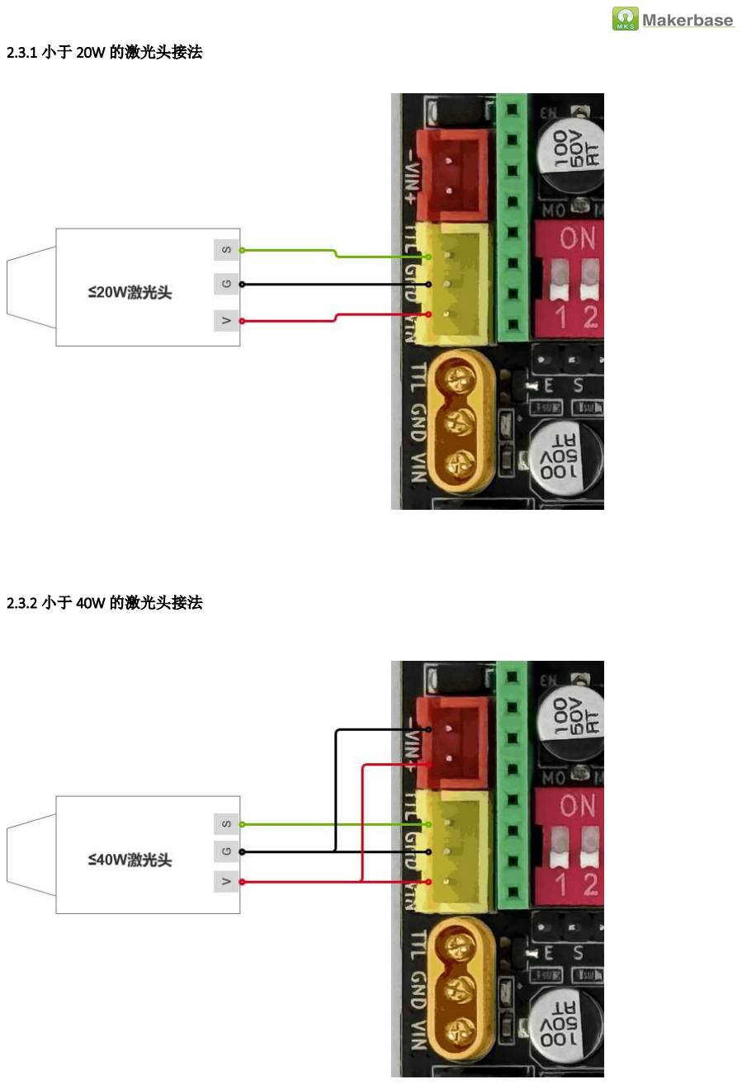
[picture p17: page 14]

2.3.1 小于 20W 的激光头接法

2.3.2 小于 40W 的激光头接法

2.3.3 小于 50W 的激光头接法

2.4 CNC 主轴接法

SPINDLE 接口：用于接主轴（直流电机），这个口为输出口，输出电压为 0-12V 或 0-24V，最大电压取

决于输入电源的电压。如电源的输入电压为 24V，则 SPINDLE 接口输出最大电压为 24V。目前主轴电机

支持最大功率为：12V 时最大支持 10W，24V 时最大支持 20W。

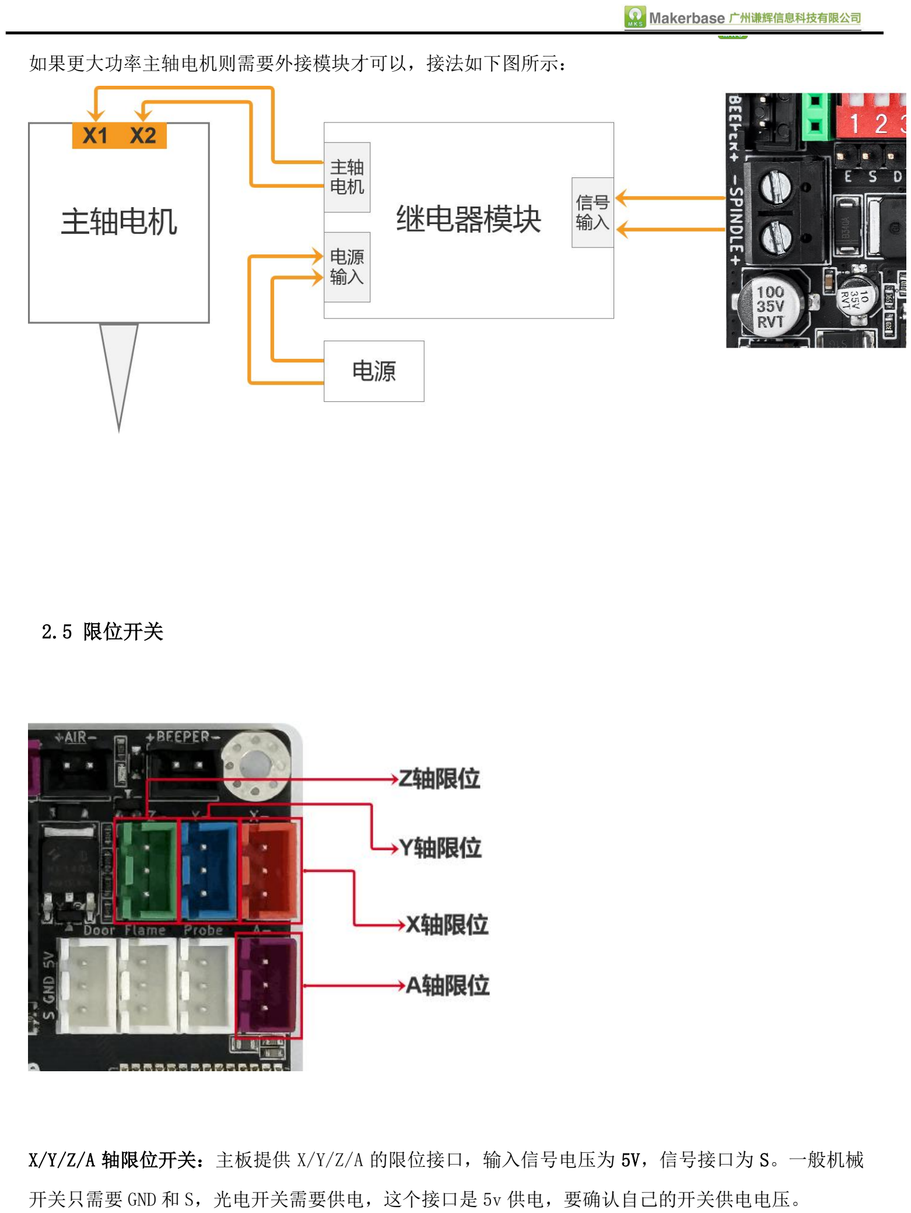
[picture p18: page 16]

如果更大功率主轴电机则需要外接模块才可以，接法如下图所示：

2.5 限位开关

X/Y/Z/A 轴限位开关：主板提供 X/Y/Z/A 的限位接口，输入信号电压为 5V，信号接口为 S。一般机械

开关只需要 GND 和 S，光电开关需要供电，这个接口是 5v 供电，要确认自己的开关供电电压。

2.6 PROBE（对刀）、安全接口

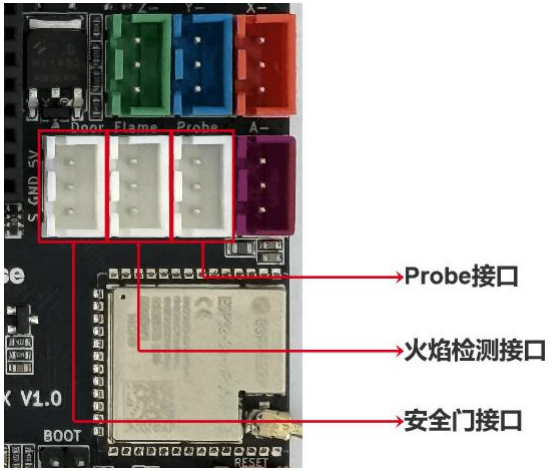
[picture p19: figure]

Probe 接口：对刀探针接口。

火焰检测接口：Flame 接口，需要外接火焰检测模块，可在配置中配置开启或者关闭。

安全门接口：开盖后触发保护机制，需要增加安全门开关，可在配置中配置开启或者关闭。

接口输入信号电压为 5V，信号接口为 S，同时提供 5V 的供电接口，可以为需要供电的模块进行供电。

2.7 蜂鸣器、空气辅助接口

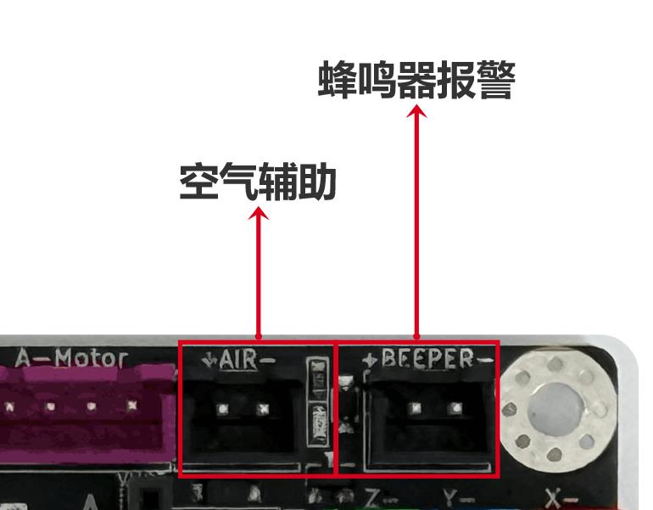
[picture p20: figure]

空气辅助：用于接气泵，可通过 M8 指令开启，M9 指令关闭。

蜂鸣器接口：这个接口与屏幕上的蜂鸣器是公用的。当前主要作用是用于触发报警时（如火焰检测触

发后），做提示作用。

### 2.8 急停开关接口：

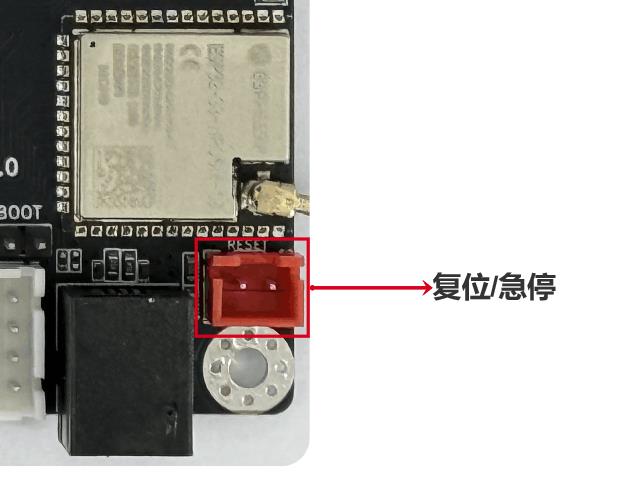
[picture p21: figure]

急停接口：短接后，会将当前所有动作立即停止。

### 2.9 屏幕、手柄接口

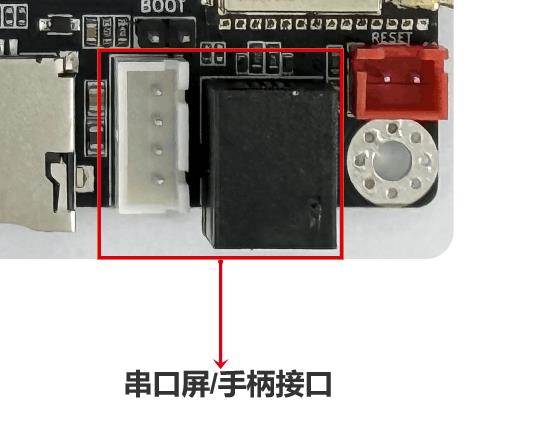
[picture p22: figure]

屏幕/手柄接口：XH2.54-4P 接口与 RJ11 接口为并联，所以只能接其中一组。

屏幕是用于激光雕刻的串口脱机雕刻屏幕， 手柄是用于 CNC 雕刻时的串口脱机雕刻。

### 2.10 TF 卡、PC 接口

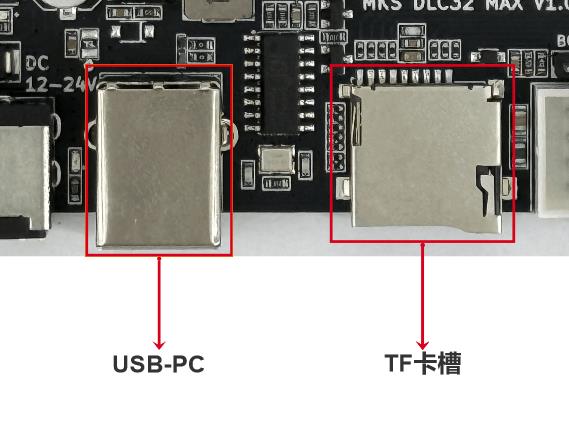
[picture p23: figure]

USB-PC 接口：USB 接口类型为 USB-B 接口，可以用于烧写程序与联机作用。

注意：这个接口是不供电的，所以需要接上 DC 电源才可以使用。USB 串口芯片是使用 CH340，所以

在使用之前请安装 CH340 驱动。

TF 卡槽：用于脱机雕刻时插卡接口，建议卡类型为：Class4 或 Class10 倍速；4~16G 内存；Fat32

格式。文件格式支持：.NC; .GC; .GCODE

## 三 . 主板参数设置

MKS DLC32 主板参数修改可以通过以下两个途径进行修改更新

1.通过网页 WEB 端进行修改参数

网页端的连接可以参考上文描述。进入 ESP32-WEB 之后，进入“setting”界面

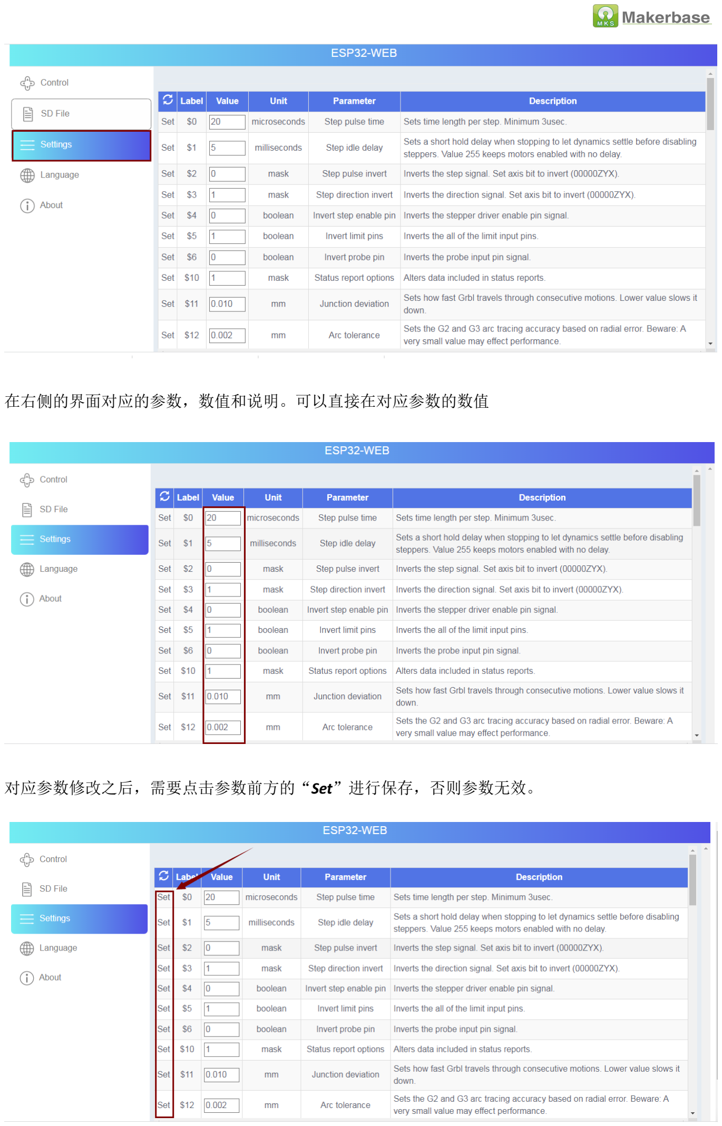
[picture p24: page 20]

在右侧的界面对应的参数，数值和说明。可以直接在对应参数的数值

对应参数修改之后，需要点击参数前方的“Set”进行保存，否则参数无效。

2.通过 PC 上位机进行修改参数

可以通过 GRBLLASER 或者 Lightburn 等软件进行读取和修改。以下为 GRBLLASER 为例。

打开 GRBLLASER 软件，设置对应的“COM”,波特率默认是 115200.

在主板已连接至 LaserGRBL，点击选择 Grbl configuration 就会进入参数设置界面。

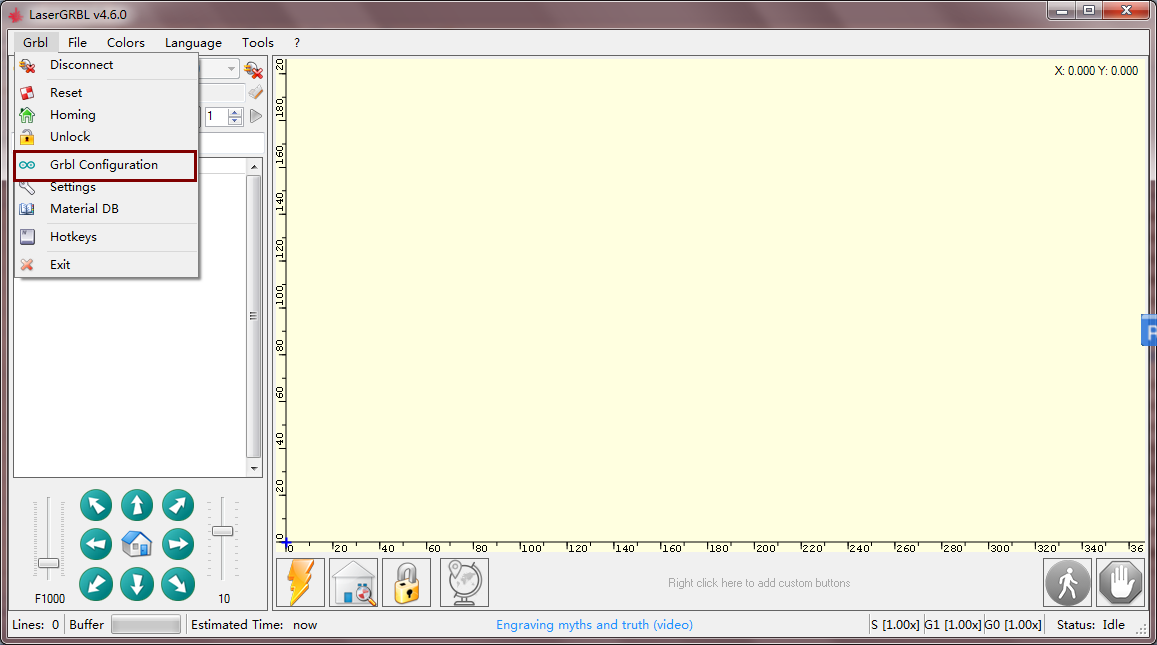
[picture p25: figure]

Grbllaser 软件参数的设置的内容和网页可以设置到的内容是一样的。

根据机器实际的情况进行修改对应的参数

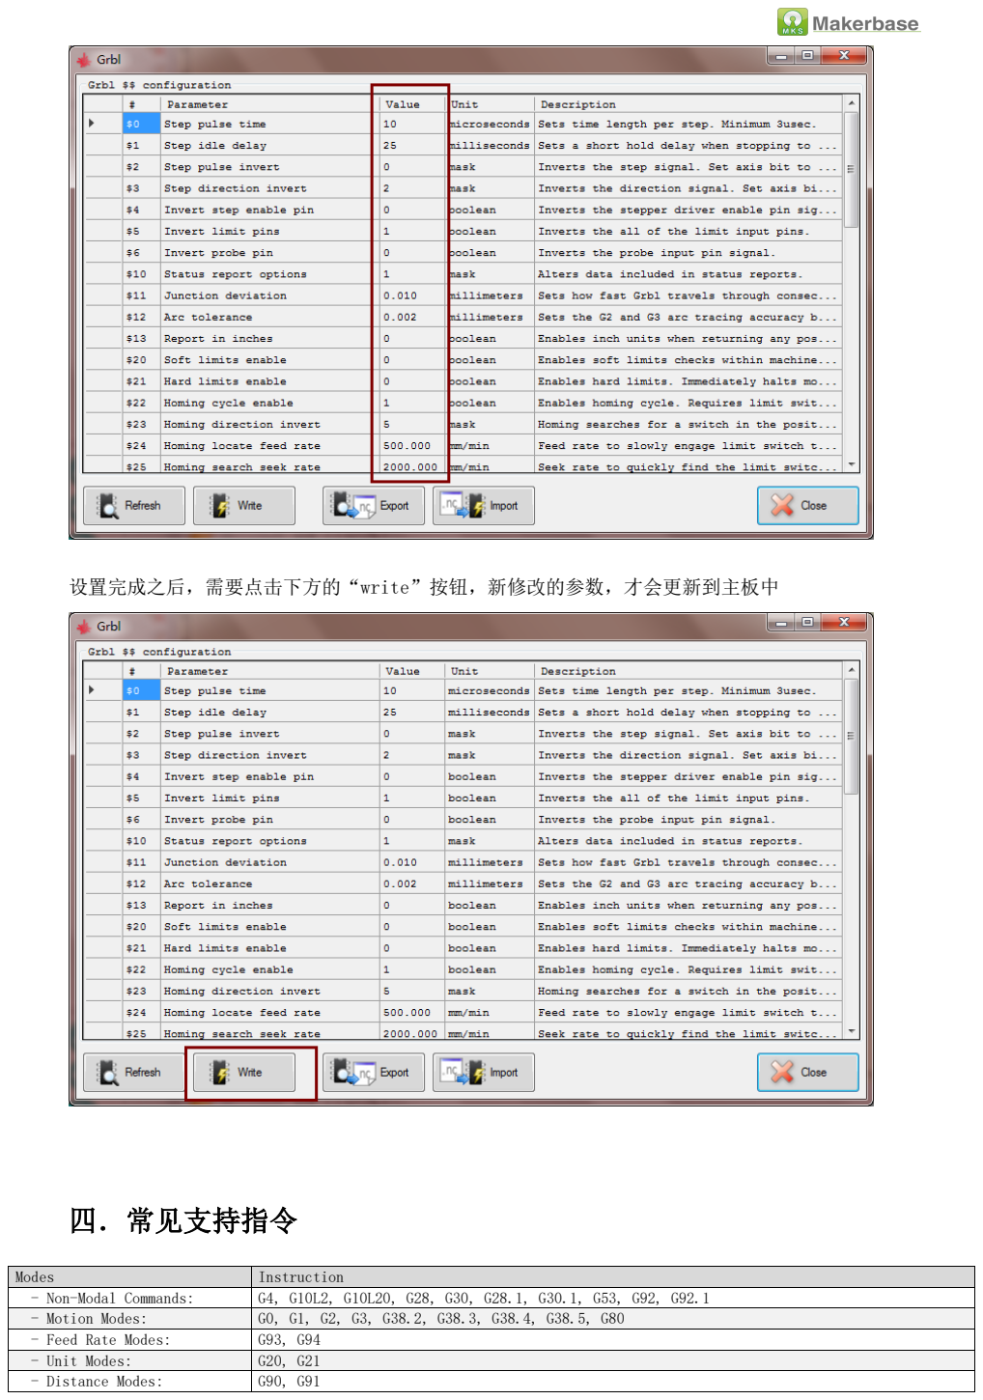
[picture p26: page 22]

设置完成之后，需要点击下方的“write”按钮，新修改的参数，才会更新到主板中

## 四．常见支持指令

Modes | Instruction
- Non-Modal Commands: | G4, G10L2, G10L20, G28, G30, G28.1, G30.1, G53, G92, G92.1
- Motion Modes: | G0, G1, G2, G3, G38.2, G38.3, G38.4, G38.5, G80
- Feed Rate Modes: | G93, G94
- Unit Modes: | G20, G21
- Distance Modes: | G90, G91

- Arc IJK Distance Modes: | G91.1
- Plane Select Modes: | G17, G18, G19
- Tool Length Offset Modes: | G43.1, G49
- Cutter Compensation Modes: | G40
- Coordinate System Modes: | G54, G55, G56, G57, G58, G59
- Control Modes: | G61
- Program Flow: | M0, M1, M2, M30*
- Spindle Control: | M3, M4, M5
- ESP32 WIFI Modes: | [ESP100],[ESP101],[ESP110],[ESP131],[ESP115],[ESP111]
[ESP100] wifi name, such as: [ESP100] MAKERBASE3D, press enter, send.
[ESP101] wifi password, such as: [ESP101] makerbase3d, press enter, send.
[ESP110] Set wifi mode, STA/AP two kinds, such as [ESP110] STA.
[ESP131] Set the connection mode. For connection, we usually set it to 8080, such as [ESP131] 8080. [ESP115] Set wifi connection and disconnection, such as [ESP115] ON, connect to wifi.
[ESP111] Get IP address

## 五．常见报错说明

错误序号 | 错误类型 | 错误提示
ERR1 | Ok | "No error"
ERR2 | ExpectedCommandLetter | "Expected GCodecommand letter"
ERR3 | BadNumberFormat | "Bad GCode number format"
ERR4 | InvalidStatement | "Invalid $ statement"
ERR5 | NegativeValue | "Negative value"
ERR6 | SettingDisabled | "Setting disabled"
ERR7 | SettingStepPulseMin | "Step pulse too short"
ERR8 | SettingReadFail | "Failed to read settings"
ERR9 | IdleError | "Command requires idle state"
ERR10 | SystemGcLock | "GCode cannot be executed in lock or alarm state"
ERR11 | SoftLimitErro | "Soft limit error"
ERR12 | Overflow | "Line too long"
ERR13 | MaxStepRateExceeded | "Max step rate exceeded"
ERR14 | CheckDoor | "Check door"
ERR15 | LineLengthExceeded | "Startup line too long"
ERR16 | TravelExceeded | "Max travel exceeded during jog"
ERR17 | InvalidJogCommand | "Invalid jog command"
ERR18 | SettingDisabledLaser | "Laser mode requires PWM output"
ERR19 | HomingNoCycles | "No Homing/Cycle defined in settings"
ERR20 | GcodeUnsupportedCommand | "Unsupported GCode command"
ERR21 | GcodeModalGroupViolation | "Gcode modal group violation"
ERR22 | GcodeUndefinedFeedRate | "Gcode undefined feed rate"
ERR23 | GcodeCommandValueNotInteger | "Gcode command value not integer"
ERR24 | GcodeAxisCommandConflict | "Gcode axis command conflict"
ERR25 | GcodeWordRepeated | "Gcode word repeated"
ERR26 | GcodeNoAxisWords | "Gcode no axis words"
ERR27 | GcodeInvalidLineNumber | "Gcode invalid line number"
ERR28 | GcodeValueWordMissing | "Gcode value word missing"
ERR29 | GcodeUnsupportedCoordSys | "Gcode unsupported coordinate system"
ERR30 | GcodeG53InvalidMotionMode | "Gcode G53 invalid motion mode"
ERR31 | GcodeAxisWordsExist | "Gcode extra axis words"
ERR32 | GcodeNoAxisWordsInPlane | "Gcode no axis words in plane"
ERR33 | GcodeInvalidTarget | "Gcode invalid target"
ERR34 | GcodeArcRadiusError | "Gcode arc radius error"
ERR35 | GcodeNoOffsetsInPlane | "Gcode no offsets in plane"
ERR36 | GcodeUnusedWords | "Gcode unused words"
ERR37 | GcodeG43DynamicAxisError | "Gcode G43 dynamic axis error"
ERR38 | GcodeMaxValueExceeded | "Gcode max value exceeded"
ERR39 | PParamMaxExceeded | "P param max exceeded"
ERR40 | FsFailedMount | "Failed to mount device"

ERR41 | FsFailedRead | "Failed to read"
ERR42 | FsFailedOpenDir | "Failed to open directory"
ERR43 | FsDirNotFound | "Directory not found"
ERR44 | FsFileEmpty | "File empty"
ERR45 | FsFileNotFound | "File not found"
ERR46 | FsFailedOpenFile | "Failed to open file"
ERR47 | FsFailedBusy | "Device is busy"
ERR48 | FsFailedDelDir | "Failed to delete directory"
ERR49 | FsFailedDelFile | "Failed to delete file"
ERR50 | BtFailBegin | "Bluetooth failed to start"
ERR51 | WifiFailBegin | "WiFi failed to start"
ERR52 | NumberRange | "Number out of range for setting"
ERR53 | InvalidValue | "Invalid value for setting"
ERR54 | MessageFailed | "Failed to send message"
ERR55 | NvsSetFailed | "Failed to store setting"
ERR56 | NvsGetStatsFailed | "Failed to get setting status"
ERR57 | AuthenticationFailed | "Authentication failed!"
ERR58 | AnotherInterfaceBusy | "Another interface is busy"
ERR59 | JogCancelled | "Jog Cancelled"

## 六．主板常见问题及其解决办法

Q1: MKS DLC32 主板上电之后，为何屏幕没有任何显示？

A1:检查主板左上侧的电源指示灯（Vin，5v，3.3v）是否正常亮灯。亮灯不正常的话，可能是供电有

问题。如果电源指示灯正常，但是屏幕不亮。可能是固件和硬件不对应，请重新选择下载更新正

确的固件，屏幕即可恢复显示

Q2：触摸屏显示不完全/白屏，这种情况如何解决？

A2: 这种情况为固件选择错误（比如，主板连接了 TS35-R，但是更新的是 TS24-R 的固件就会出现这

种情况），重新更新正确的固件即可恢复。

Q3: MKS DLC32 主板更新固件之后按照到雕刻机后，方向不对应需要怎么修改？

A3：可通过上位机软件，或者网页参数配置界面，修改“$3”的数值，参考下表

指令：$2，$3，$23 | 参数
X+ Y+ Z+ | 0

Q4: MKS DLC32（cnc 模式下），z 轴无法回零？

A4:默认的情况下，主板是没有使能 z 轴回零的。可将主板连接到 PC 上位机软件，然后发送对应的命

令进行使能，$Homing/Cycle1=Z（使能 z 轴回零），$Homing/Cycle1=0（取消轴回零）。

注：z 轴回零功能暂仅适用于 CNC 版本的固件。

## 七 . 技术支持及保证

1. 发货前会做通电测试，保证可以正式使用才发货。
2. 欢迎各位朋友加入讨论群：650031716
3. 欢迎光临博客交流：https://blog.csdn.net/gjy_skyblue
4. 固件 GITHUB 的链接：https://github.com/makerbase-mks/MKS-DLC32
5. 激光主板，3D 打印机主板可定制化，联系：黄生 13148932315 | 谭生 15521395023 | 蔡生 13726298657
6. 有问题可联系我们客服或者在群里找技术支持人员，我们将竭诚为您服务

### 创客基地淘宝

X- Y+ Z+ | 1
X+ Y- Z+ | 2
X- Y- Z+ | 3
X+ Y+ Z- | 4
X- Y+ Z- | 5
X+ Y- Z- | 6
X- Y- Z- | 7

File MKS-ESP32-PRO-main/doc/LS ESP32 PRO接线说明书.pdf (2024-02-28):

# LS ESP32 PRO 接线说明书

## QQ 群：650031716

## 修改时间：2023 -05

目录

## 一．主板概述及特点


LS ESP32 PRO V1.1 主板,是一款专为桌面雕刻机开发的脱机雕刻主控板。采用 ESP32 双核 32 位超强

CPU，主频高达 240MHz。使用静音 TMC2209 驱动，最高速度达到 30000mm/s，3.5 寸屏幕脱机雕刻，支

持远程 WIFI，远程蓝牙控制，APP 控制和 PC 端 WEB 控制。激光长时间停留同点，激光头倾斜，火焰检

测，安全门等多重保护，非常适合桌面雕刻机使用。

## 二、外观及接口示意图

## 三、主板基础参数

## 主要硬件指标

板卡型号 | LS ESP32 PRO V1.1
电源输入 | 12V~24V 10A
激光头最大功率 | 50W
CPU 型号 | ESP32
核心处理器 | 双核 32 位处理器
主频 | 240M HZ
RAM | 348KB
ROM | 8M
电机驱动 | TMC2209
驱动电流 | 最大 1.5A
WIFI-PC 端 | 支持
蓝牙-APP 端 | 支持
WIFI-APP 端 | 支持
滚轴驱动 | 支持
脱机雕刻 | 支持，3.5 寸触摸屏
安全门 | 支持
空气冷却 | 支持
激光头停留保护 | 支持
切斜保护 | 支持（外加陀螺仪检测模块）
烟雾报警 | 支持（外加烟雾检测模块）
蜂鸣器报警 | 支持（外接蜂鸣器）
急停功能 | 支持
雕刻速度 | <=30000mm/s

## 四、主板尺寸图


## 五、烧录软件的安装于说明与固件烧录

## 注意：LS ESP32 PRO 必须使用 “MKSLaserTool V2.X”版本以上才可以烧写！！！

### 5.1 软件安装与连接

解压文件后，打开文件目录下，找到“ MKSLaserTool_setupV2.x.x.exe”并且双击打开，进入安装过 程。


安装 USB 驱动文件（CH340），如果 PC 之前已经安装过该文件则不需要重复安装。
安装完成之后，可将 MKS DLC32 主板通过 USB 线连接至 PC，在 PC 设备管理中，查看主板是否有被分配相 应的 COM。正常分配则主板已连接上 PC,如果没有显示的话，请重新检查软件的安装，和硬件的连接是否 存在问题。


主板在连接 USB 到 PC 时，同时需要连接 12-24v 进行供电，如果未连接 12-24v 供电，主板将无法别识 别。
如下图，为连接后，com 正确识别。


### 5.2 软件介绍与固件烧录

点击“MKS ESP32 Download Tool”，进入烧写界面

### 1.打开需要烧写的固件，文件格式为 bin。 2. COM:可在设备管理器中，查看到具体的 COM 序号，按照实际情况进行设置。BAUD：波特率一

## 般建议选择 115200。 3.ESP32 型号：LS ESP32 PRO 主板需要选择“ESP32 S3”，否则会烧写失败。

### 4.设置好参数后，开始烧写固件。

## 六、主板接口明细说明

## 6.1 电源输入


DC 电源接口：该接口可接 12V 或者 24V 电源，最大承受电流 10A，电源输入端子为“DC-007B-

### 2.1mm”接口。

外接电源开关：可以用来外接开关来控制电源。注意：这个接口不是电源输入接口，切记不能接电

源。

### 6.2 USB-PC 接口


USB-PC 接口：USB 接口类型为 USB-B 接口，可以用于烧写程序与联机作用。

注意：这个接口是不供电的，所以需要接上 DC 电源才可以使用。USB 串口芯片是使用 CH340，所以在使

用之前请安装 CH340 驱动。

### 6.3 TF 卡槽


TF 卡槽：用于脱机雕刻时插卡接口，建议卡类型为：Class4 或 Class10 倍速；4~16G 内存；Fat32 格 式。文件格式支持：.NC; .GC; .GCODE

## 6.4 常用功能接口


### 6.4.1 串口屏接口：用于外接脱机屏幕，使用 RJ11 接口，可在配置中配置开启或者关闭。

### 6.4.2 状态灯显示：

红色：报警指示灯
黄色：故障指示灯
绿色：蓝牙状态设备正常工作
浅蓝色蓝色：WIFI-AP 状态设备正常工作
深蓝色蓝色：WIFI-STA 状态设备正常工作

### 6.4.3 复位按键外接端口：用于复位 MCU 或者当作紧急停止按键。

### 6.4.4 火焰检测：Flame 接口，需要外接火焰检测模块，可在配置中配置开启或者关闭。

### 6.4.5 倾斜保护：机器倾斜保护功能，需要外接倾斜检测模块，可在配置中配置开启或者关闭。

### 6.4.6 安全门保护：开盖后触发保护机制，需要增加安全门开关，可在配置中配置开启或者关闭。

### 6.4.7 Z 轴限位：可以作为自动对焦的触发开关，需要开启 Z 轴自动对焦功能。

### 6.4.8 强制烧写模式：长按这个按键后，再开机，可以强制进入烧写模式。

### 6.5 . 蜂鸣器报警、空气冷却输出


外接蜂鸣器：当触发保护功能后，可触发蜂鸣器报警，可在配置中配置开启或者关闭。 空气冷却输出：空气辅助功能，可在配置中配置开启或者关闭。

### 6.6. 电机输出


X 轴电机：驱动为 TMC2209 驱动，默认电流为 1.2A，计算公式：I=V，建议最大不要超过 1.6A。

Y1/Y2 电机：驱动为 TMC2209 驱动，默认电流为 1.2A，计算公式：I=V，建议最大不要超过 1.6A。

Z 轴电机/驱动：这个轴为滚轴驱动，$45:0 为普通模式，1 为滚轴模式。

TMC2209 高速模式：建议默认为高速模式，雕刻效果更佳。

6.6.1 . 电机线序说明


步进电机接口说明：1A 与 1B 为同一组线序，2A 与 2B 为同一组线序，可用万用表测试电机上的线序， 相通的就为一组。

### 注意：一定要在拔掉电源情况下，再插拔驱动或者电机，避免烧坏驱动。

### 6.7 . 激光头接法


## 12/24V 常开接口：12/24V 常开输出，也可以作为激光头一路功能。 激光头输出接口 1- XH2.54-2P：可以接 20W 以下的激光头，也可以与上面 12/24V 并联 接较大的激光头，可达 40W。 激光头输出接口 2- MR30PB-M 公头 ：可以接 50W 以下激光头，信号与 XH2.54 为并

联。

## 七、配置参数说明

### 7.1 常用参数指令

指令 | 参数 | 描述
$0 | 10 | Sets time length per step. Minimum 3usec.
$1 | 5 | Sets a short hold delay when stopping to let dynamics settle before disabling steppers. Value 255 keeps motors enabled with no delay.
$2 | 0 | Inverts the step signal. Set axis bit to invert (00000ZYX).
$3 | 1 | Inverts the direction signal. Set axis bit to invert (00000ZYX).
$4 | 0 | Inverts the stepper driver enable pin signal.
$5 | 1 | Inverts the all of the limit input pins.
$6 | 0 | Inverts the probe input pin signal.
$10 | 1 | Alters data included in status reports.
$11 | 0.01 | Sets how fast Grbl travels through consecutive motions. Lower value slows it down.
$12 | 0.002 | Sets the G2 and G3 arc tracing accuracy based on radial error. Beware: A very small value may effect performance.
$13 | 0 | Enables inch units when returning any position and rate value that is not a settings value.
$20 | 0 | Enables soft limits checks within machine travel and sets alarm when exceeded. Requires homing.
$21 | 0 | Enables hard limits. Immediately halts motion and throws an alarm when switch is triggered.
$22 | 0 | Enables homing cycle. Requires limit switches on all axes.
$23 | 0 | Homing searches for a switch in the positive direction. Set axis bit (00000ZYX) to search in negative direction.
$24 | 300 | Feed rate to slowly engage limit switch to determine its location accurately.
$25 | 1000 | Seek rate to quickly find the limit switch before the slower locating phase.
$26 | 250 | Sets a short delay between phases of homing cycle to let a switch debounce.
$27 | 1 | Retract distance after triggering switch to disengage it. Homing will fail if switch isn't cleared.
$30 | 1000 | Maximum spindle speed. Sets PWM to 100% duty cycle.
$31 | 0 | Minimum spindle speed. Sets PWM to 0.4% or lowest duty cycle.
$32 | 1 | Enables laser mode. Consecutive G1/2/3 commands will not halt when spindle speed is changed.
$100 | 80 | X-axis travel resolution in steps per millimeter.
$101 | 80 | Y-axis travel resolution in steps per millimeter.
$102 | 80 | Z-axis travel resolution in steps per millimeter.
$110 | 6000 | X-axis maximum rate. Used as G0 rapid rate.
$111 | 6000 | Y-axis maximum rate. Used as G0 rapid rate.
$112 | 6000 | Z-axis maximum rate. Used as G0 rapid rate.
$120 | 500 | X-axis acceleration. Used for motion planning to not exceed motor torque and lose steps.
$121 | 500 | Y-axis acceleration. Used for motion planning to not exceed motor torque and lose steps.
$122 | 500 | Z-axis acceleration. Used for motion planning to not exceed motor torque and lose steps.
$130 | 285 | Maximum X-axis travel distance from homing switch. Determines valid machine space for soft-limits and homing search distances.
$131 | 272 | Maximum Y-axis travel distance from homing switch. Determines valid machine space for soft-limits and homing search distances.
$132 | 80 | Maximum Z-axis travel distance from homing switch. Determines valid machine space for soft-limits and homing search distances.

### 7.2 附加参数指令

$40 | 1 | 设置语言， 0 为中文，1 为英文
$41 | 1 | 蜂鸣器报警功能, 使用 BEEP 接口, 0 为关闭，1 为打开，默认为 1 。
$42 | 0 | 安全门保护功能，使用 Probe 接口，0 为关闭，1 为开启，默认为 0。
$43 | 0 | 火焰检测功能，使用 Flame 接口，0 为关闭，1 为打开，默认为 0。
$44 | 0 | 空气冷却功能，使用 AIR 接口，0 为关闭，1 位打开，默认为 0。
$45 | 0 | 切换滚轴功能，0 为普通模式使用 Y 轴为常规轴，1 为滚轴模式使用 Z 轴为滚轴。
$46 | 1 | 波特率设置，1 为 115200，2 为 250000。
$50 | 0 | WIFI 模式设置，0 为关闭 WIFI，1：AP 模式，2：STA 模式。
$51 | ESP_WIFI | AP 模式下的热点名称
$52 | 12345678 | AP 模式下的热点密码

$53 | My_SSID | STA 模式下的需连接的热点名称
$54 | My_password | STA 模式下的需连接的热点密码

## 八、 技术支持及保证

1. 发货前会做通电测试，保证可以正式使用才发货。
2. 欢迎各位朋友加入讨论群：650031716
3. 欢迎光临博客交流：https://blog.csdn.net/gjy_skyblue
4. 固件 GITHUB 的链接：https://github.com/makerbase-mks/MKS-DLC32
4. 激光主板，3D 打印机主板可定制化，联系：黄生 13148932315 | 谭生 15521395023 | 蔡生 13726298657

彭生 13427595835

5. 有问题可联系我们客服或者在群里找技术支持人员，我们将竭诚为您服务


创客基地官网 | 创客基地淘宝

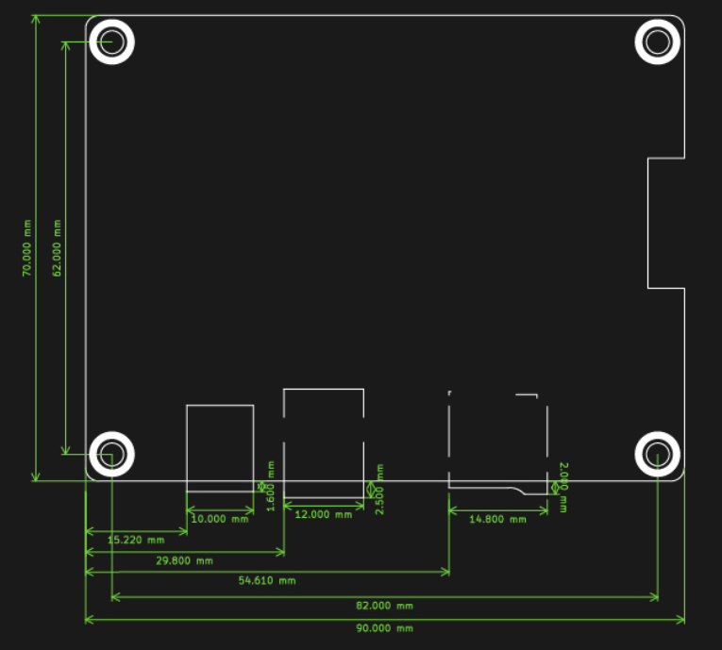
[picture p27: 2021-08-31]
MKS-DLC32-main/images/size_board.png

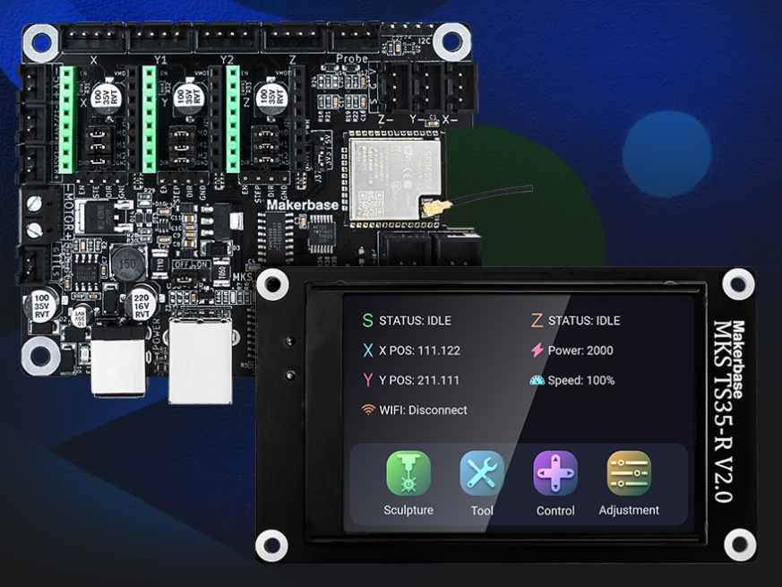
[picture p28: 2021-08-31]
MKS-DLC32-main/images/main.png

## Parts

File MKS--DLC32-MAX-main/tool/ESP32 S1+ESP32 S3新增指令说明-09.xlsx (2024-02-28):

S1方案新增指令表
指令 | 功能 | 默认值 | 使能说明 | 检测逻辑 | 响应状况 | 使用接口 | 备注
$41 | 蜂鸣器 | 1 | 0：关闭；1：使能 | 按照具体触发功能报警 | 按照具体触发功能报警 | BEEP接口
$42 | 安全门检测 | 0 | 0：关闭；1：高灵敏度触发；2低灵敏度触发。 | 高灵敏度：每500ms检测一次，Probe引脚拉低1s后触发报警。 低灵敏度：每1000ms检测一次，Probe引脚拉低2s后触发报警。 | 蜂鸣器响3s停1s，循环5次后，就直接关闭报警。 | Probe接口
$43 | 火焰检测 | 0 | 0：关闭；1：高灵敏度触发；2低灵敏度触发。 | 高灵敏度：每500ms检测一次，Flame引脚拉低1s后触发报警。 低灵敏度：每1000ms检测一次，Flame引脚拉低2s后触发报警。 | 蜂鸣器响3s停1s，循环5次后，就直接关闭报警。 | Flane接口
$44 | 空气冷却 | 0 | 0：关闭； 1：使能气泵功能，并且最小值为0%输出； 2：使能气泵功能，并且最小值为5%输出； | 默认M8启动气泵，M9关闭气泵 | 发M8指令后启动气泵，M9关闭气泵。 使能1时，发M9指令后，完全关闭输出。 使能2时，发M9指令后，不完全关闭输出，还需要输出5%。 | AIR接口
$45 | Y轴与滚轴切换 | 0 | 0：使用Y轴；1：使用滚轴；2：Z轴自动对焦 | 0：Y轴/1：Z轴/2:Y轴+Z轴（对焦轴） | 0时输出Y轴电机，1时输出Z轴电机，2时输出Y轴电机与Z轴电机 | Y轴/Z轴 |  | 参数为1，移动滚轴，移 动完会再次移动一段距离
$46 | 修改串口波特率 | 1 | 1:115200,2:250000 | 使用该波特率连接电脑上位机 | 正确波特率才可以通讯 | USB-PC
$47 | 串口屏使能 | 0 | 0：屏蔽串口屏；1：开启串口屏 | 开启后才可以接脱机串口屏 | 开启后才可以接脱机串口屏 | RJ11
$50 | WIFI模式 | 0 | 0：关闭WiFi； 1：Wifi切换为AP模式； 2：Wifi切换为STA模式 |  |  | ESP32模块
$51 | WiFi AP模式热点名称 | MKS_DLC | 最少1个字符，最多32个字符 |  |  | -
$52 | WiFi AP模式热点密码 | 12345678 | 最少8个字符，最多64个字符 |  |  | -
$53 | WiFi STA模式连接热点名称 | MKS_DLC | 最少1个字符，最多32个字符 |  |  | -
$54 | WiFi STA模式连接热点密码 | 12345678 | 最少8个字符，最多64个字符 |  |  | -
$101 | Y轴脉冲 | 80 |  |  |  | -
$102 | 滚轴脉冲 | 100 |  | 切换到滚轴时所使用的脉冲值 |  | -
$453 | 自动对焦高度 | 10 | 可配置范围5mm~100mm | G28 Z0指令进行回零Z轴。其他G28指令不需要回零 | 触发Z轴限位后，回弹的Z轴高度，参考CNC对刀的功能。
S3方案新增指令表
指令 | 功能 | 默认值 | 使能说明 | 检测逻辑 | 响应状况 | 使用接口 | 备注
$40 | 5V可控接口 | 0 | 0：关闭；1：使能 | 使能1后，直接就常输出这个IO口后就可以了。 | 根据配置来输出 | 5V可控接口
$41 | 蜂鸣器 | 1 | 0：关闭；1：使能 | 按照具体触发功能报警 | 按照具体触发功能报警 | BEEP接口
$42 | probe检测功能 | 0 | 0：关闭；1：高灵敏度触发；2低灵敏度触发。 | 高灵敏度：每500ms检测一次，Probe引脚拉低1s后触发报警。 低灵敏度：每1000ms检测一次，Probe引脚拉低2s后触发报警。 | 蜂鸣器响3s停1s循环5次后，停2s重新循环报警 | Probe接口 |  | 没有循环报警
$43 | 火焰检测 | 0 | 0：关闭；1：高灵敏度触发；2低灵敏度触发。 | 高灵敏度：每500ms检测一次，Flame引脚拉低1s后触发报警。 低灵敏度：每1000ms检测一次，Flame引脚拉低2s后触发报警。 | 蜂鸣器响3s停1s循环5次后，停2s重新循环报警 | Flane接口 |  | 没有循环报警
$44 | 空气冷却 | 0 | 0：关闭； 1：使能气泵功能，并且最小值为0%输出； 2：使能气泵功能，并且最小值为5%输出； | 默认M8启动气泵，M9关闭气泵 | 发M8指令后启动气泵，M9关闭气泵。 使能1时，发M9指令后，完全关闭输出。 使能2时，发M9指令后，不完全关闭输出，还需要输出5%。 | AIR接口
$45 | Y轴与滚轴切换 | 0 | 0：使用Y轴；1：使用滚轴；2：Z轴自动对焦 | 0：Y轴/1：Z轴/2:Y轴+Z轴（对焦轴） | 0时输出Y轴电机，1时输出Z轴电机，2时输出Y轴电机与Z轴电机 | Y轴/Z轴
$46 | 修改串口波特率 | 1 | 1:115200,2:250000 | 使用该波特率连接电脑上位机 | 正确波特率才可以通讯 | USB-PC
$47 | 串口屏使能 | 0 | 0：屏蔽串口屏；1：开启串口屏 | 开启后才可以接脱机串口屏 | 开启后才可以接脱机串口屏 | RJ11
$48 | 安全门 | 0 | 0：关闭；1：高灵敏度触发；2低灵敏度触发。 | 高灵敏度：每500ms检测一次，Door引脚拉低1s后触发报警。 低灵敏度：每1000ms检测一次，Door引脚拉低2s后触发报警。 |  | Door接口 |  | 没有循环报警
$50 | WIFI模式 | 0 | 0：关闭WiFi； 1：Wifi切换为AP模式； 2：Wifi切换为STA模式 3：蓝牙模式 |  |  | ESP32模块 |  | 电脑搜索不到蓝牙设备
$51 | WiFi AP模式热点名称 | MKS_DLC | 最少1个字符，最多32个字符 |  |  | -
$52 | WiFi AP模式热点密码 | 12345678 | 最少8个字符，最多64个字符 |  |  | -
$53 | WiFi STA模式连接热点名称 | MKS_DLC | 最少1个字符，最多32个字符 |  |  | -
$54 | WiFi STA模式连接热点密码 | 12345678 | 最少8个字符，最多64个字符 |  |  | -
$101 | Y轴脉冲 | 80 |  |  |  | -
$102 | 滚轴脉冲 | 100 |  | 切换到滚轴时所使用的脉冲值 |  | -
$453 | 自动对焦高度 | 10 | 可配置范围5mm~100mm | G28 Z0指令进行回零Z轴。其他G28指令不需要回零 | 触发Z轴限位后，回弹的Z轴高度，参考CNC对刀的功能。

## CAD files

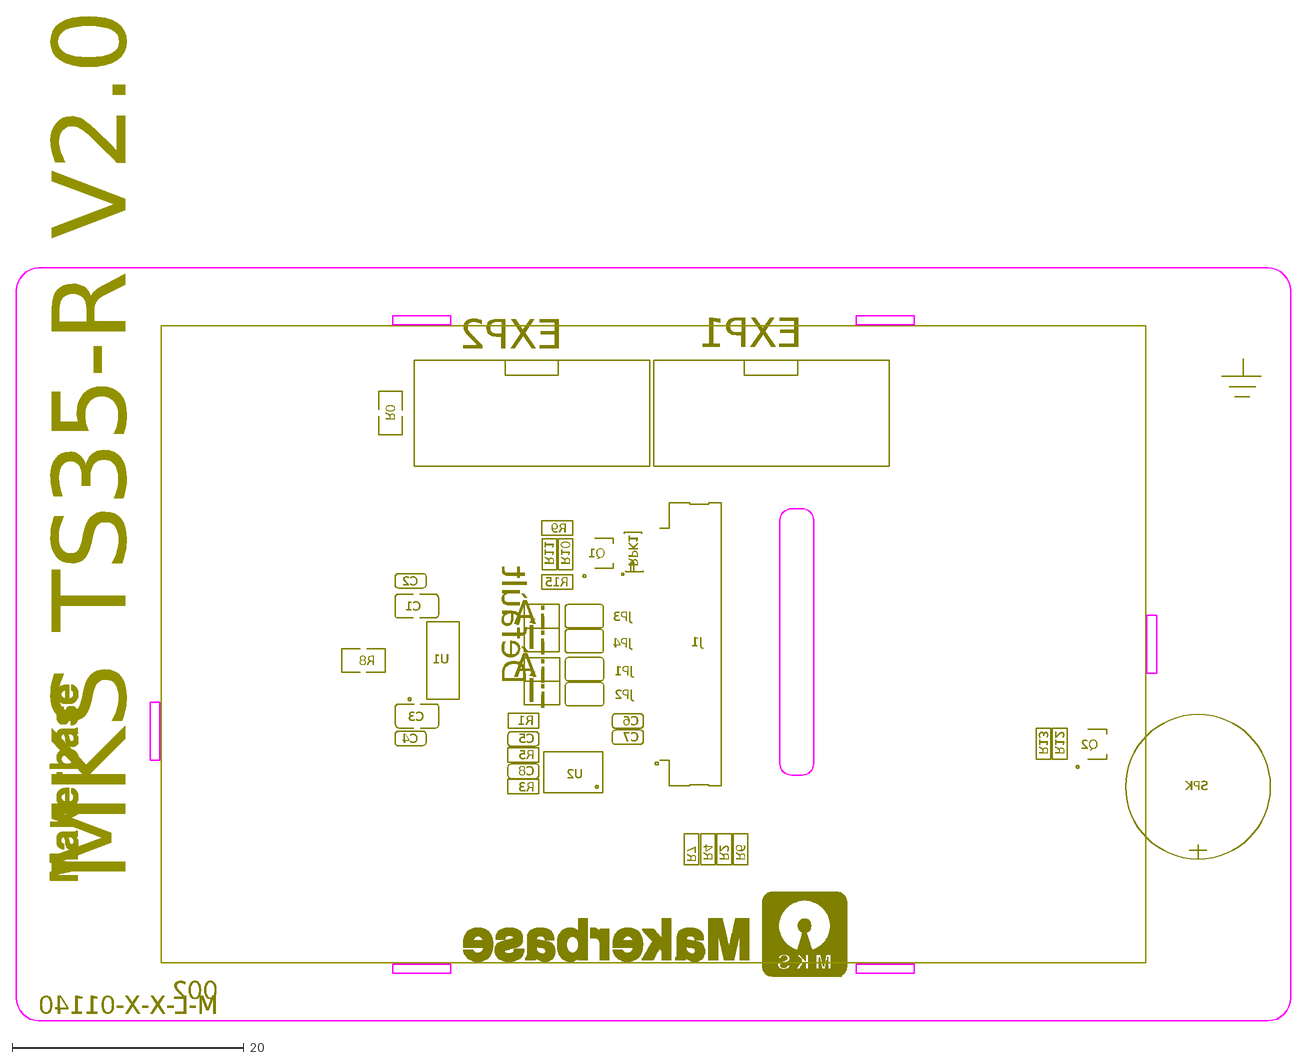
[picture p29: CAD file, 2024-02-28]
MKS-DLC32-main/hardware/MKS TS35-R.DXF
MKS TS35-R V2.0
Default
¡Ì
¡Á
002
M-L-X-X-01140
R15
C1
C2
C3
C4
C5
C6
C7
C8
EXP1
EXP2
Q1
Q2
R1
R2
R3
R4
R5
R6
R7
R8
R9
R10
R11
R12
R13
RPK1
SPK
U1
U2
J1
JP1
JP2
JP3
JP4
R0

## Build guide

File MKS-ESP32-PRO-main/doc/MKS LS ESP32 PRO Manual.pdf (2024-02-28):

# MKS LS ESP32 PRO Manual

## Date：2023 -09

# Directory

Overview and Features---------------------------------------------------------------------------------------------------------3 Hardware parameters-----------------------------------------------------------------------------------------------------3 Installation Dimensions--------------------------------------------------------------------------------------------------- 4 LS ESP32 PRO Operation -------------------------------------------------------------------------------------------------------5 Connect the motherboard interface ----------------------------------------------------------------------------------- 5 Update the motherboard firmware. ----------------------------------------------------------------------------------- 8 Install MKS LASERTOOL and USB driver files (ch340) ---------------------------------------------------------8 Firmware update operation ---------------------------------------------------------------------------------------10 Use of mainboard control -----------------------------------------------------------------------------------------------12 PC HOST-software control ----------------------------------------------------------------------------------------- 12 Wireless connection control ---------------------------------------------------------------------------------------13 APP CONTROL ---------------------------------------------------------------------------------------------------------18 Modify the parameters of the motherboard. ---------------------------------------------------------------------- 23

# Overview and Features

LS ESP32 PRO V1.1 motherboard is specially developed for desktop engraving machines. Using ESP32 dual-core 32-bit super CPU, the main frequency is as high as 240MHz.

Integrated silent TMC2209 driver, the maximum working speed reaches 30000mm/min
3.5 inch screen offline engraving
Support WIFI, Bluetooth connection. It can be controlled by APP and PC-side WEB. Multi-link protection mechanism, laser stays at the same point for a long time, laser head tilt, flame detection, safety door and other

multiple protections, very suitable for desktop engraving machines. Hardware parameters

Board Module | LS ESP32 PRO V1.1
Power input | 12V~24V 10A
Max Power | 50W
CPU Module | ESP32
Main frequency | 240M HZ
RAM | 348KB
ROM | 8M
Motor Drive | TMC2209（Maximum current 1.5A）
WIFI-PC | Support
Bluetooth-APP | Support
WIFI-APP | Support
Roll axis | Support
Offline engraving | Support（work with 3.5inch touch screen）
Security door alarm | Support
Air assisted | Support
Laser stay alarm | Support
Laser tilt alarm | Support（External Gyroscope Module）
Smoke alarm | Support（External smoke detection module）
Buzzer expansion | Support
Emergency stop button extension | Support
Engraving speed | <=30000mm/min

### Installation Dimensions

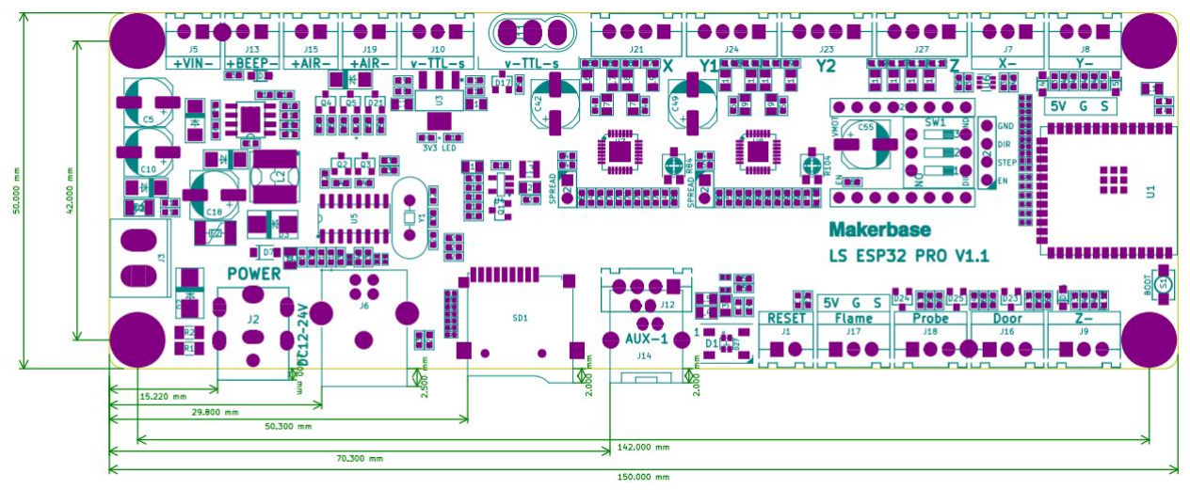
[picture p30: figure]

# LS ESP32 PRO Operation

When you get the LS ESP32 PRO motherboard. The operation is divided into the following three parts. 1. Connect the motherboard interface. 2. Update the motherboard firmware. 3. Use of mainboard control. 4. Modify the parameters of the motherboard. Connect the motherboard interface

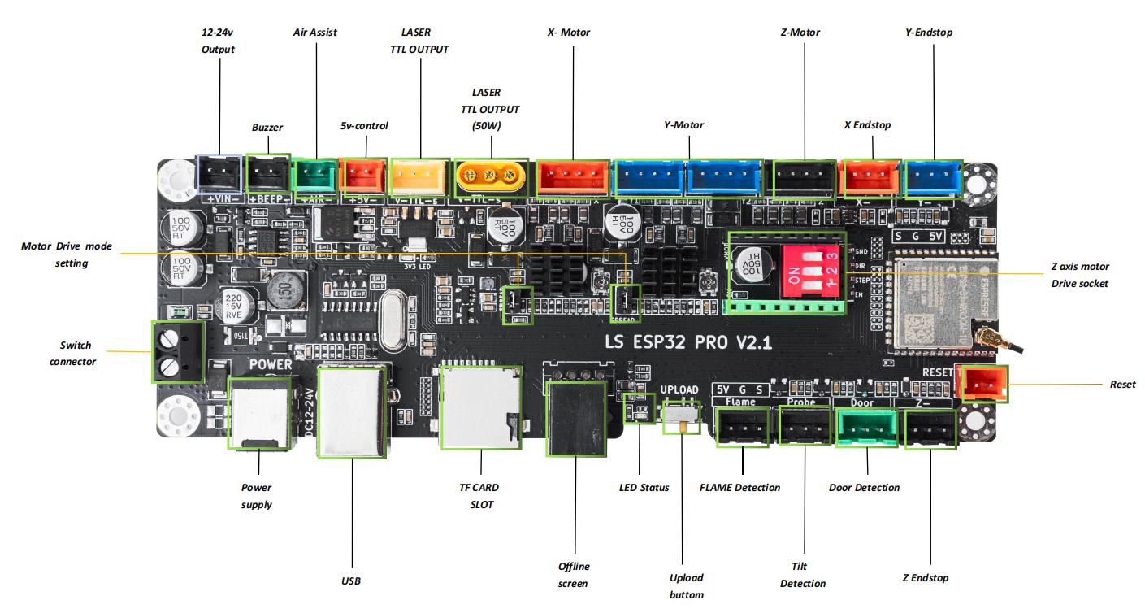
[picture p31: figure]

Power supply：Voltage 12-24v, maximum current 10A, connector model: "DC-007B-2.1mm" Switch connector：Used for external switches to control power on and off. (Note: The default is disconnected. If the switch is not connected, please connect the + and - of the interface to ensure normal power

supply.)

USB Port: Connect to PC for firmware update and host computer control
（Note：The mainboard serial port chip is CH340. Before connecting to the PC, please install the corresponding USB driver file on the PC so that the mainboard can be recognized normally.The USB interface does not have a 5v power supply. When connecting to a PC, it is mainly necessary to connect a 12-24v power supply so that the PC can recognize the motherboard.）

TF Card Slot：Connect the TF card. Store engraving files.The recommended card type is: Class4 or Class10 speed; 4~16G memory; Fat32 format. File format support: .NC; .GC; .GCODE

Offline Screen：Connect to MKS exclusive touch screen, control, engrave and other operations through the screen，Screen connector type is RJ11

Led Staus：Reflect the current status of the motherboard
Red: alarm indicator
Yellow: fault indicator light

Green: Bluetooth status The device is working
Light blue Blue: WIFI-AP status The device is working
Dark blue blue: WIFI-STA status device is working

Reset：Used to reset the MCU or an external emergency stop button. Flame Detection：Connect the flame detection sensor. Features can be enabled in firmware. Tilt Delection：Connect the tilt detection sensor. Features can be enabled in firmware. Door Delection：Connect the machine safety door switch, if the safety door is opened during the working process, the work will be

suspended.Features can be enabled in firmware

BOOT:Press this button often, the motherboard will be forced into the programming mode. (Normally updating firmware doesn't need to use it). It can be used only when the motherboard cannot update the firmware. X/Y/Z endstop：For connecting the endsop switch. When connecting, pay attention to the corresponding signal. If your switch only has haul with two wires, then please connect "s" and

"g"

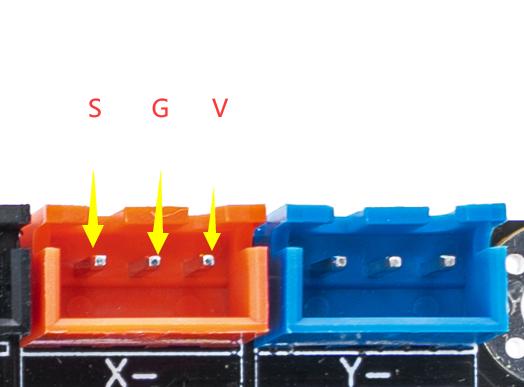
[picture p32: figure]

Z Motor socket：If the machine needs to use the z-axis, please connect the motor drive to this socket. Drivers such as A4988, TMC2208, TMC2209 can be used. If the machine does not have a z-axis by default, it is not necessary to connect. X/Y/Z Motor interface：For connecting stepper motors. The X and Y axes are driven by integrated tmc2209. The default current is 1.2A, the calculation formula: I=V, it is recommended not to exceed 1.6A

There are two motor interfaces on the Y-axis, they are connected in parallel and share the same tmc2209 drive. Z-axis motor/driver: This axis can be used as a roller drive, $45:0 （normal mode）, $45:1 roller mode. The motor interfaces of xyz are 1A-1B-2A-2B. Among them, 1A-1B is one phase of the stepping motor, and 2A-2B is the other phase of the stepping motor. (If the phase sequence of the motor connection is incorrect, the motor will not rotate normally)

Note: Be sure to plug and unplug the driver or motor when the power is off to avoid burning the driver.

Laser TTL Output：To connect the laser module, you need to pay attention to the corresponding connection of the signal. S----TTL of connecting laser

G----Connect to the gnd of the laser

V-----connect to the Vin of the laser (12-24v)
The signals of ports 1 and 2 in the picture are the same. the power of the connected laser is lower than 20W. Can be directly connected to interface 1. (connection terminal model: XH2.54-3P)

the power of the laser is connected to 20-50W. It is recommended to connect to interface 2 (connection terminal signal: MR30PB-M)

If the power of the laser module used is greater than 50w, we recommend an external power supply. The motherboard only connects "S" and "G" as control signals. Vin is externally powered separately, not connected to the "V" of the

motherboard.

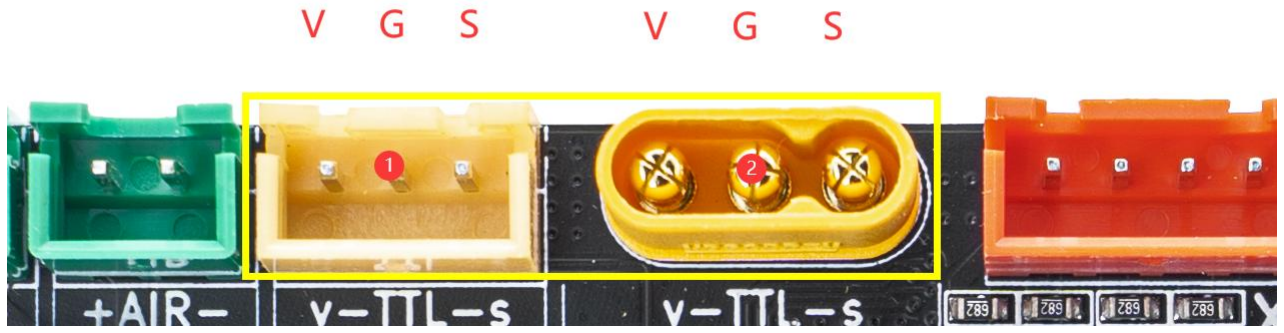
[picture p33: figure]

Air assit：Connect air-assisted equipment. BEEP: Connect the buzzer

### Install MKS LASERTOOL and USB driver files (ch340)

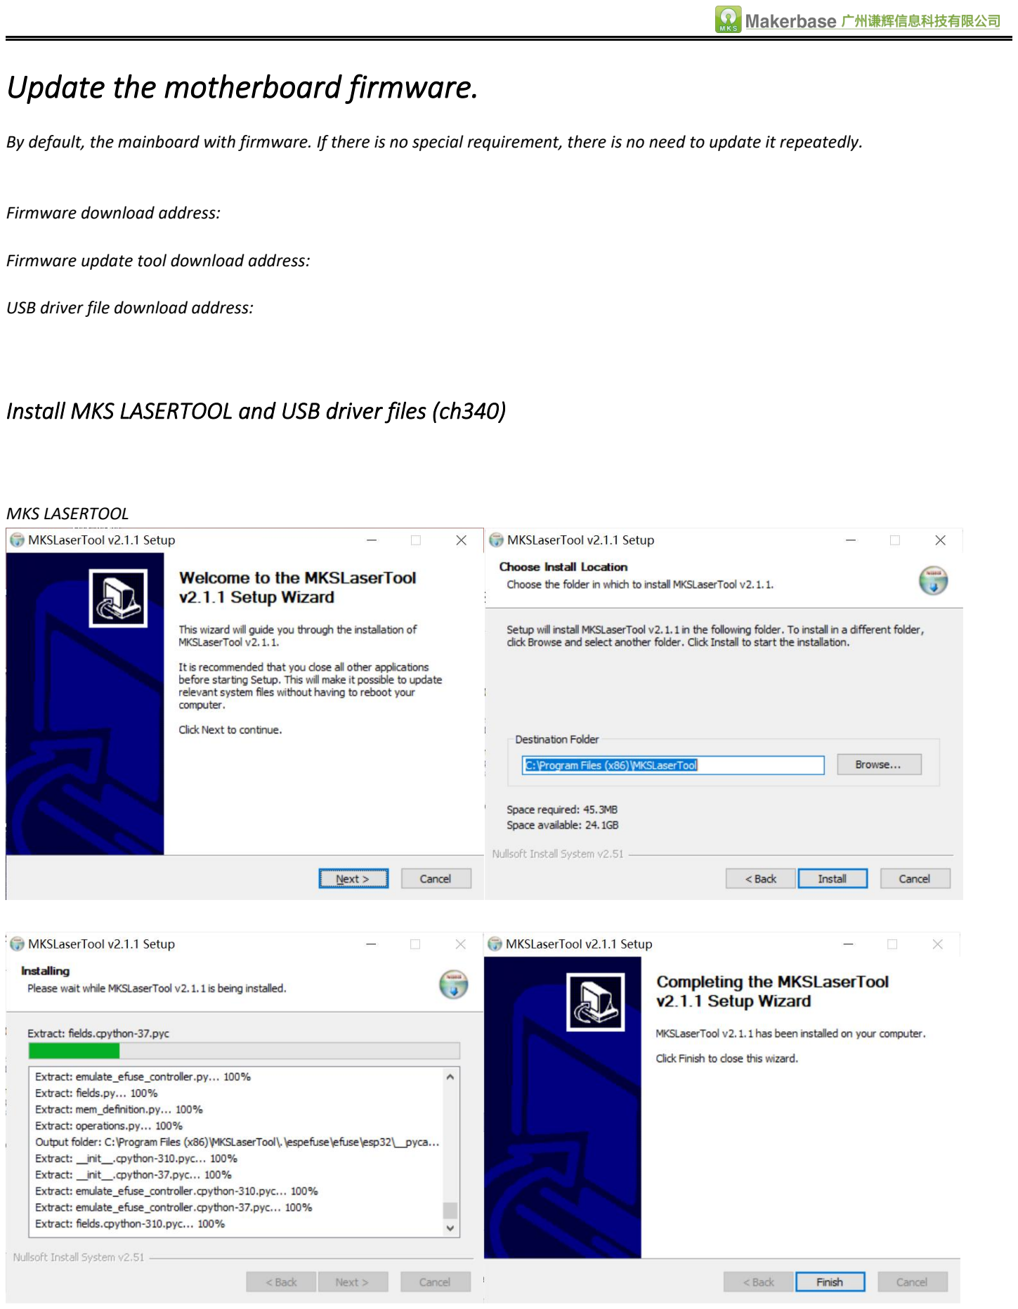
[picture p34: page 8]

Update the motherboard firmware. By default, the mainboard with firmware. If there is no special requirement, there is no need to update it repeatedly. Firmware download address:

Firmware update tool download address:

USB driver file download address:

MKS LASERTOOL

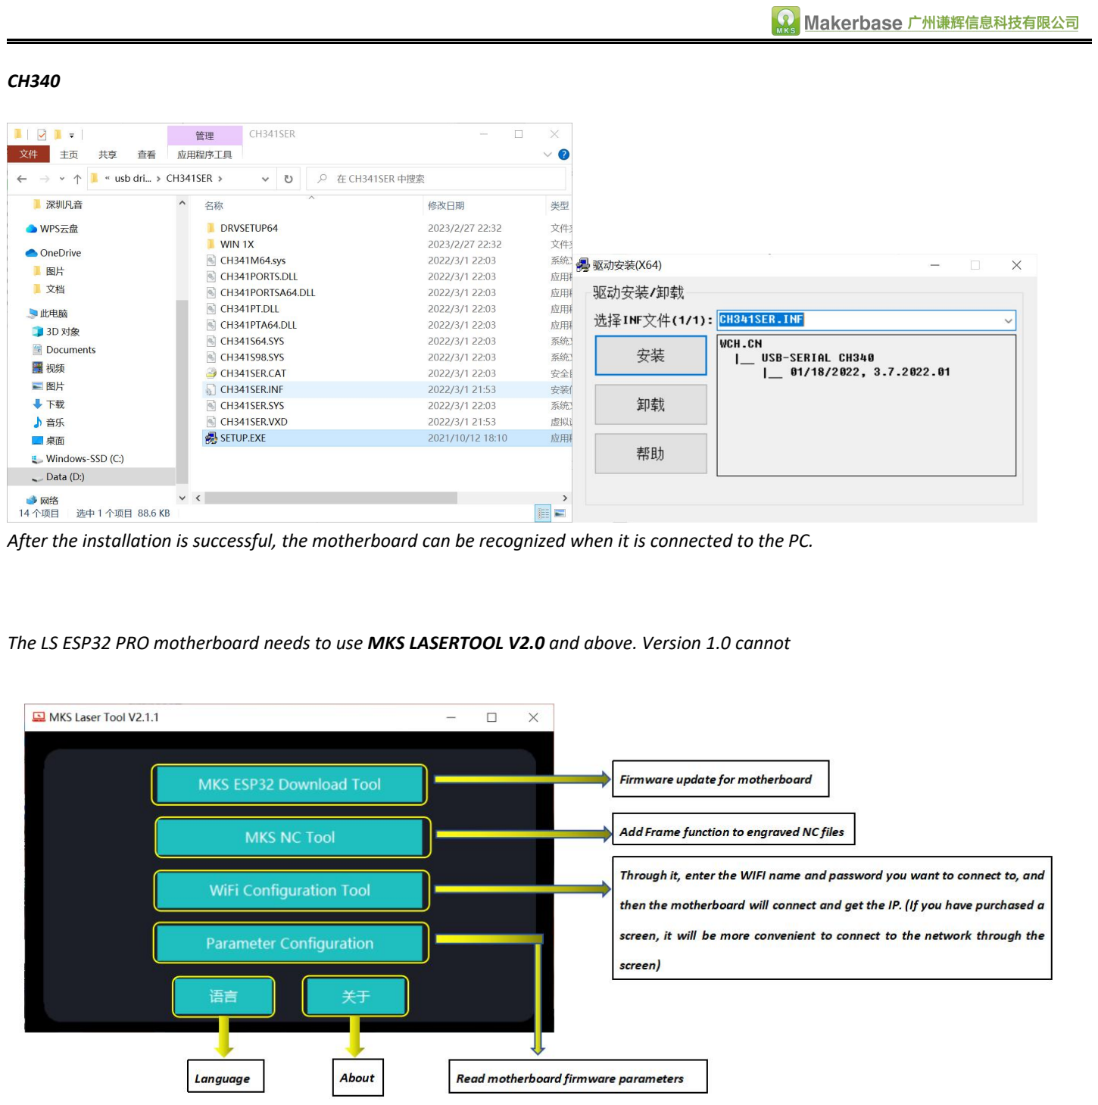
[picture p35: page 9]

CH340

After the installation is successful, the motherboard can be recognized when it is connected to the PC. The LS ESP32 PRO motherboard needs to use MKS LASERTOOL V2.0 and above. Version 1.0 cannot

### Firmware update operation

1. Connect the motherboard to the PC. Note: The usb of the motherboard is only for communication and has no power supply function, so connect 12-24v power supply at the

same time. The "switch interface" is disconnected by default, and a switch needs to be connected. If there is no switch, you can use a wire to short it, so that the motherboard will be powered on.

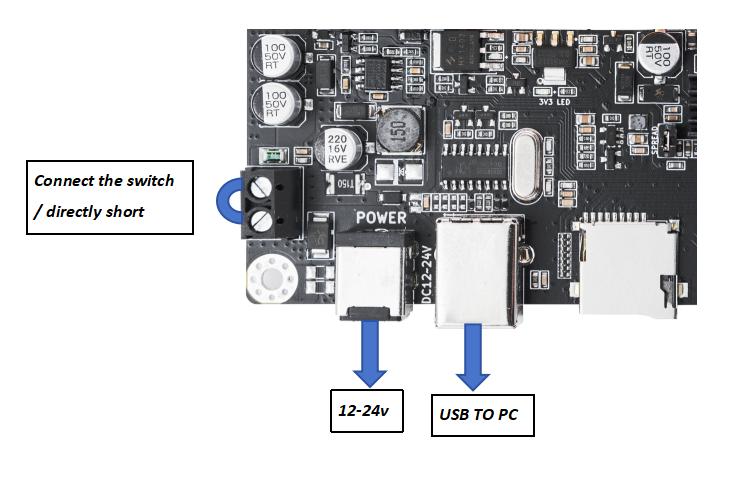
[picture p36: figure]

2, Open the MKS LASERTOOL software

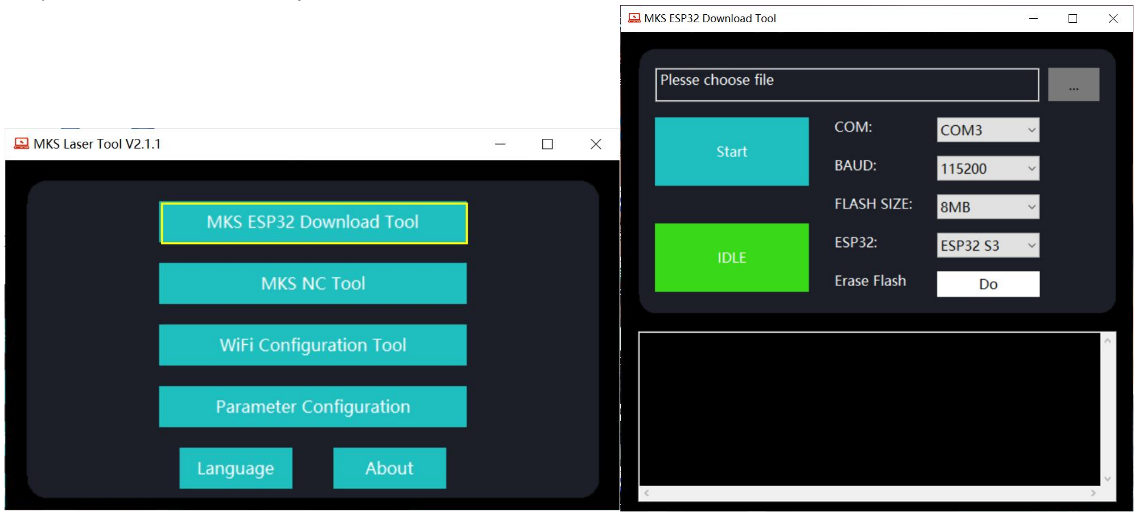
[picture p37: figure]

Please choose file: Select the bin file you downloaded corresponding to the mainboard from github

COM: By default, it will be automatically recognized, and the drop-down option selects the COM corresponding to the motherboard. If there is no option in the pull-down menu, the possible reasons are: 1. The motherboard is not powered. 2. The USB cable of the motherboard is not connected properly. 3. The ch340 driver file is not installed. BAUD: Baud rate, recommended to choose 115200

FLASH SIZE: Select 8MB

ESP32: Select esp32 s3

Erase Flash: Do

After the setting is complete, click Start to start the update

# Use of mainboard control

MKS LS ESP32 PRO has three control methods:
1. PC HOST-software control
2. Wireless connection control
3. APP control

### PC HOST-software control

LS ESP32 PRO motherboard is used for LASER and CNC control. Generally, it is recommended to use LASERGRBL, Lightburn, and other software on PC. The picture uses Lasergrbl as an example, com: Select the serial number assigned by the PC to the motherboard (it is the same as the COM for firmware update above, and will

only be displayed after the ch340 driver file is installed).The baud rate is generally 115200

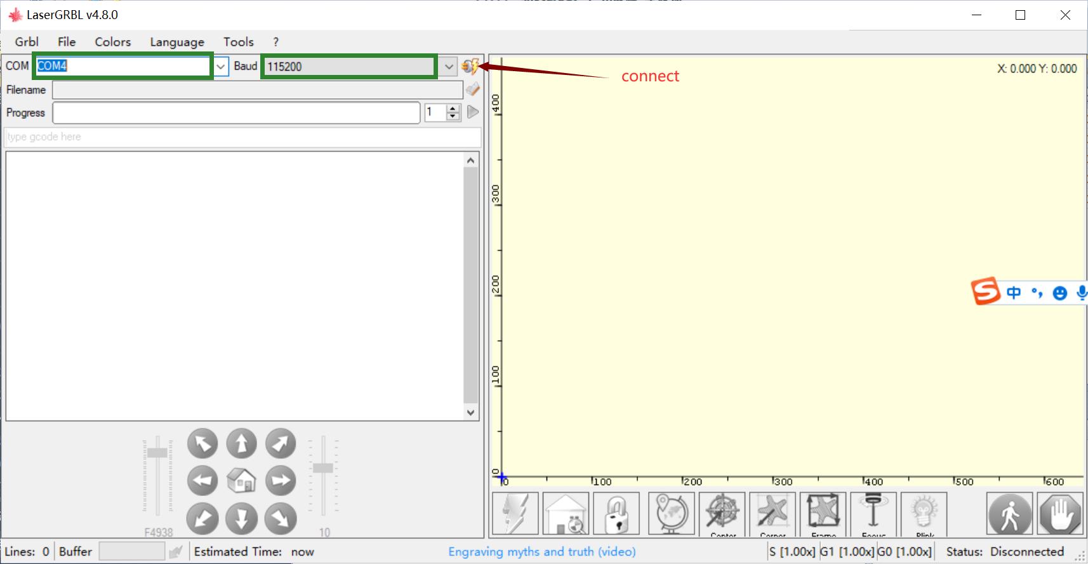
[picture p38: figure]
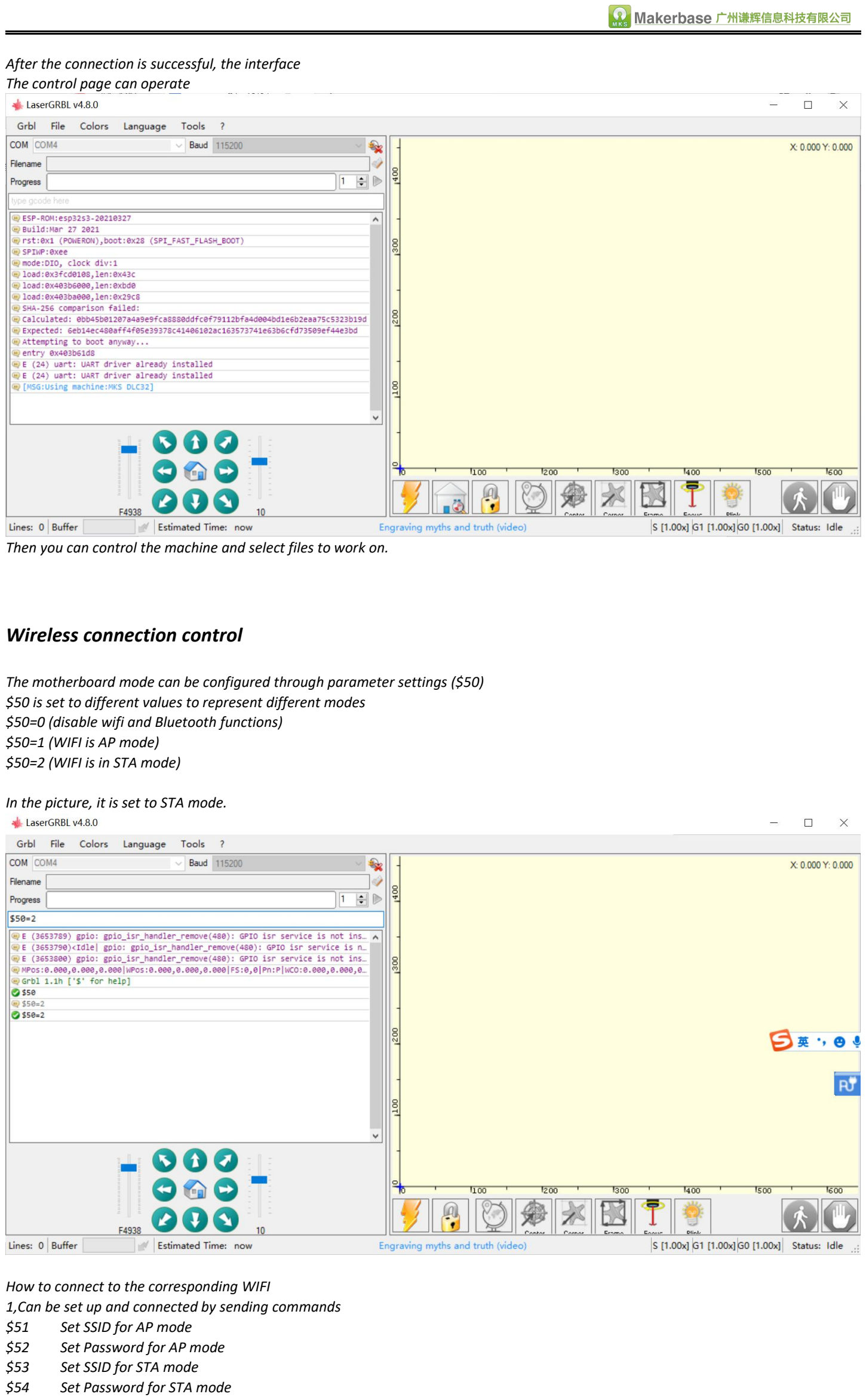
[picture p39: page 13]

After the connection is successful, the interface The control page can operate

Then you can control the machine and select files to work on. Wireless connection control

The motherboard mode can be configured through parameter settings ($50) $50 is set to different values to represent different modes
$50=0 (disable wifi and Bluetooth functions)
$50=1 (WIFI is AP mode)
$50=2 (WIFI is in STA mode)

In the picture, it is set to STA mode.

How to connect to the corresponding WIFI
1,Can be set up and connected by sending commands
$51 | Set SSID for AP mode
$52 | Set Password for AP mode
$53 | Set SSID for STA mode
$54 | Set Password for STA mode

You can set the wifi to STA mode first ($50=2)
Then set up a wireless SSID and password for $53 and $54. After the setting is completed, send $50=2 once. If the network is normal and the password is correct, the connection will be made, as

shown in the figure.

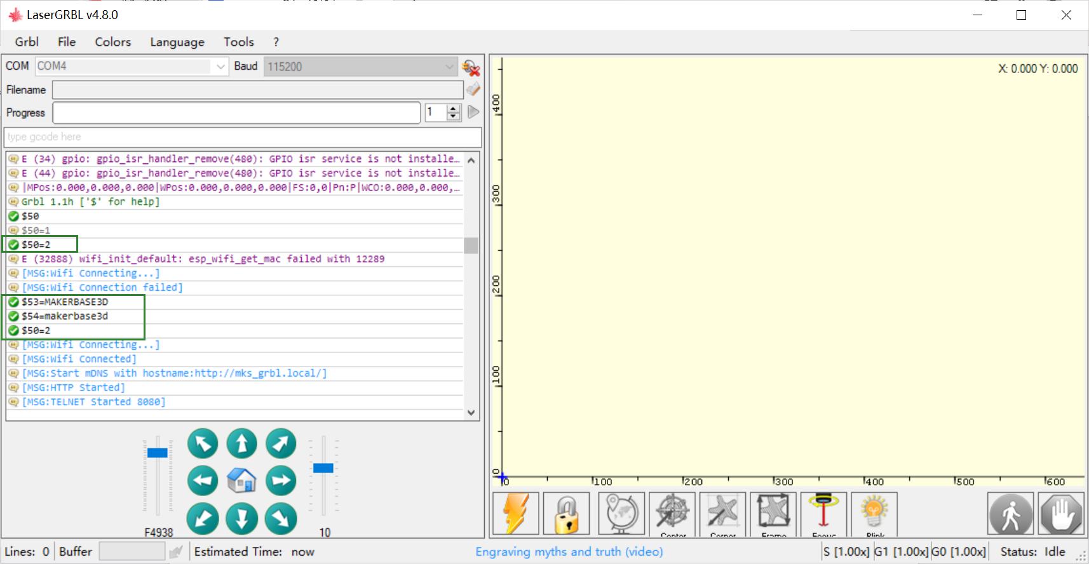
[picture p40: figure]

After the connection is successful, you can send [ESP111], Get the IP of the motherboard

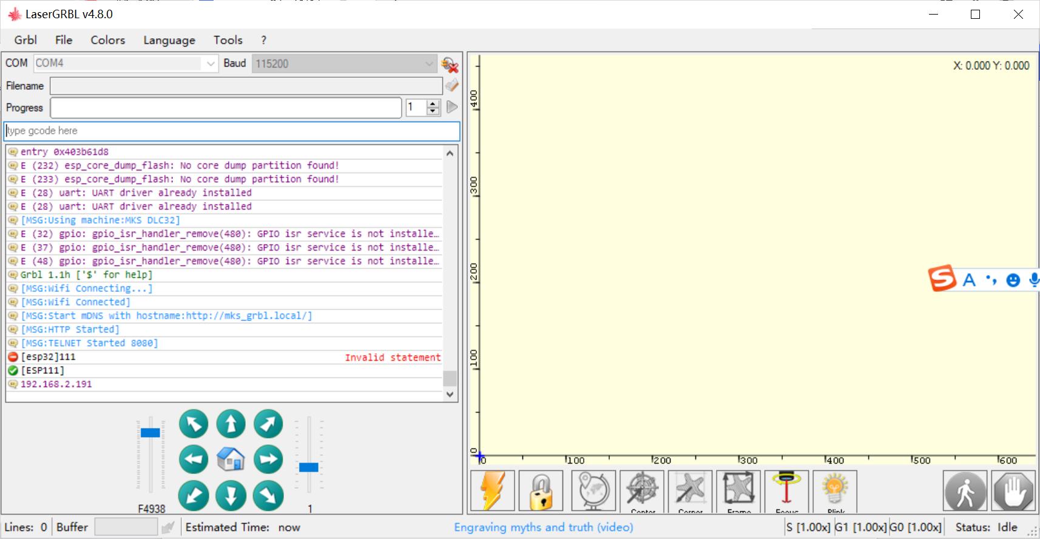
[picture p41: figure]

Then you can enter the obtained IP through the browser of your PC or mobile phone, and then you can enter the network control page. (Note that the PC or mobile phone must be connected to the same network as the motherboard before it can be connected. If it is a

different network, it cannot be connected)

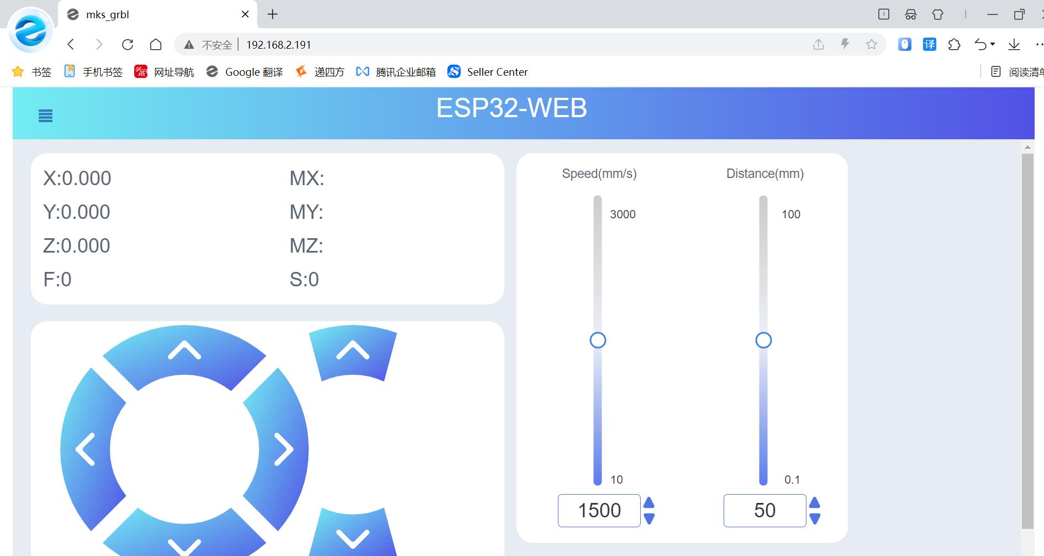
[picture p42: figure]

The motherboard can then be controlled and engraved.。

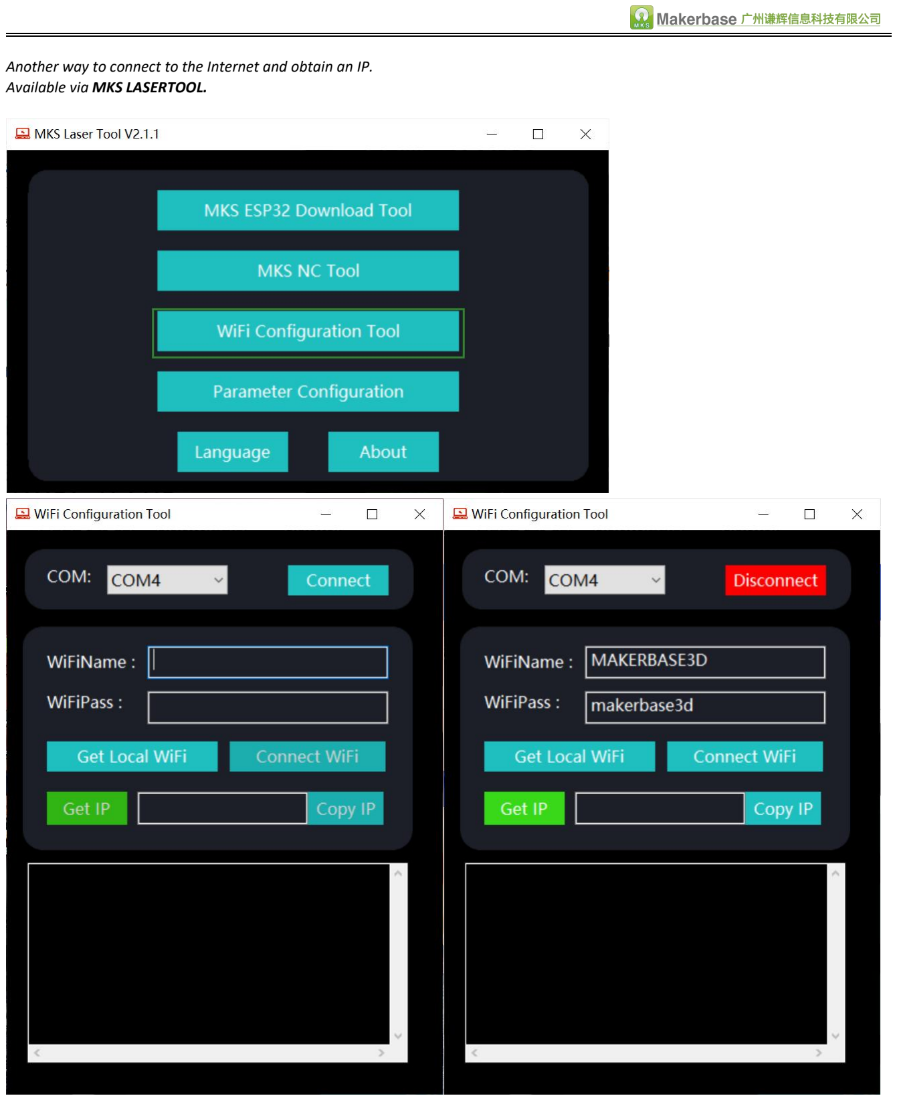
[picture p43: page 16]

Another way to connect to the Internet and obtain an IP. Available via MKS LASERTOOL.

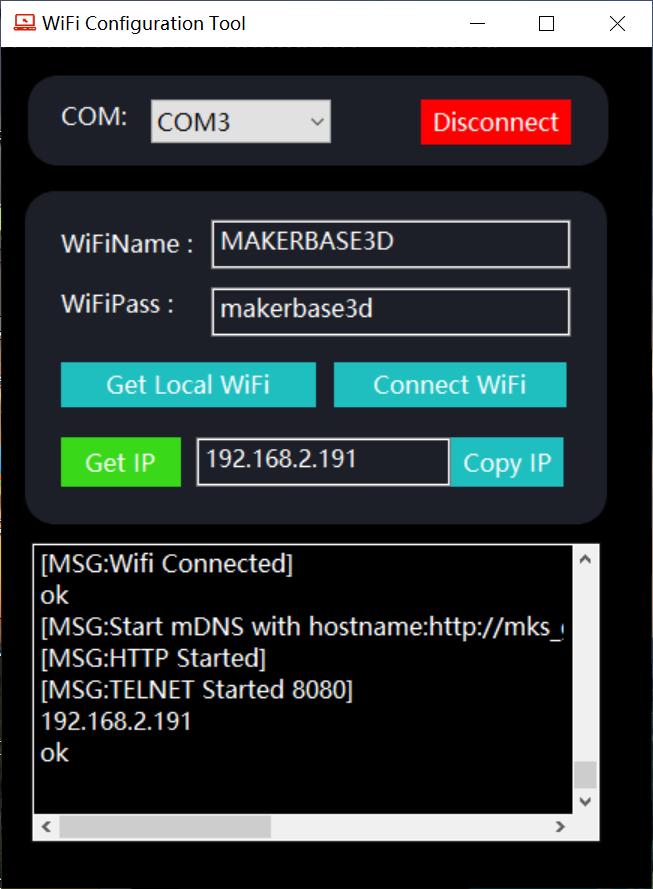
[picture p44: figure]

After setting up, click on the link wifi
After the command window below is connected, you can get the Get IP

After obtaining the IP, you can enter the IP through the browser to control the web page as described above.

## APP CONTROL

You can download our MKSLaser on the APP store or GOOGLE store

Open the APP and click the connect button in the upper left corner，Enter the IP and click Connect（The network connected to the mobile phone must be the same as the network connected to the motherboard.）

Then you can control it through the APP and engrave files.

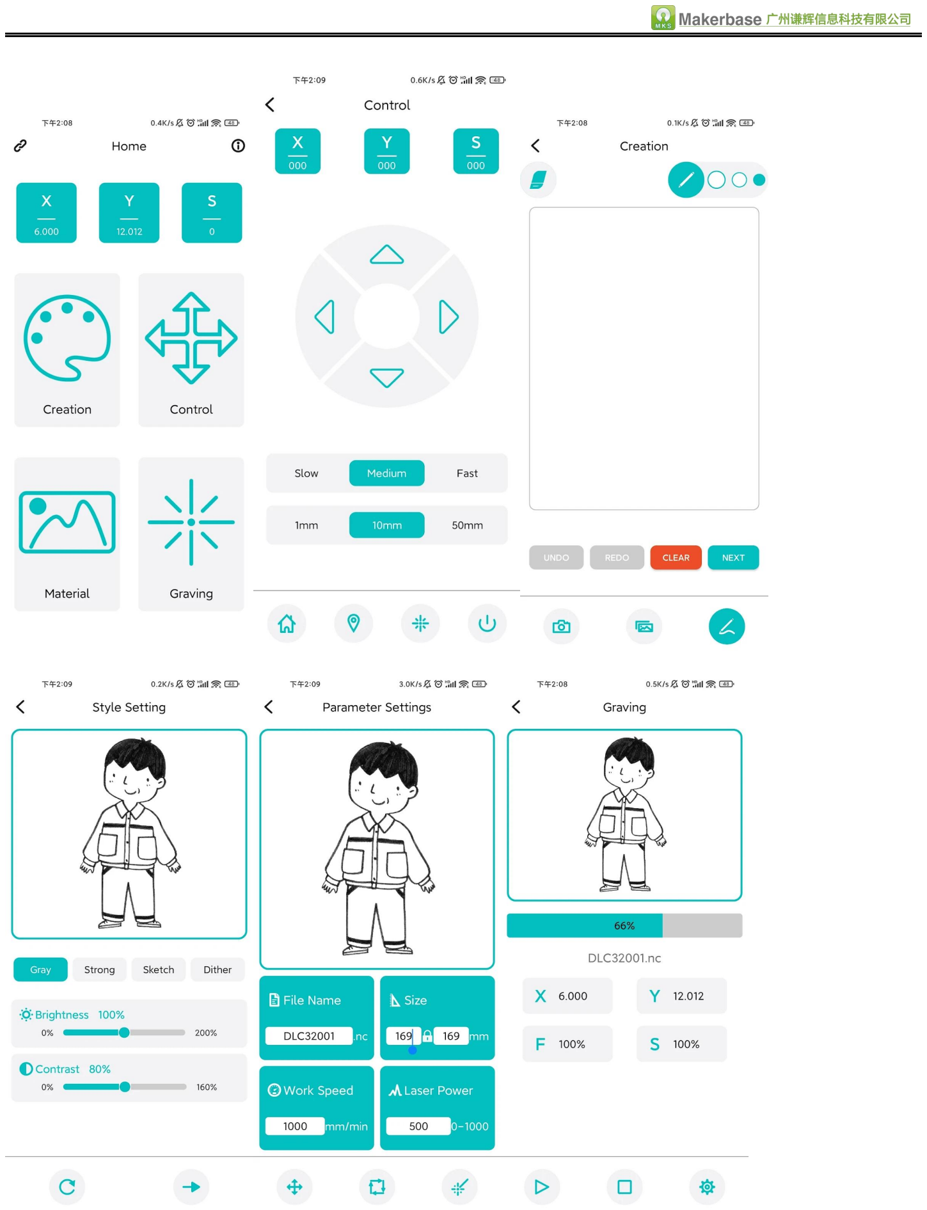
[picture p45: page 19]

## MKS touch screen control

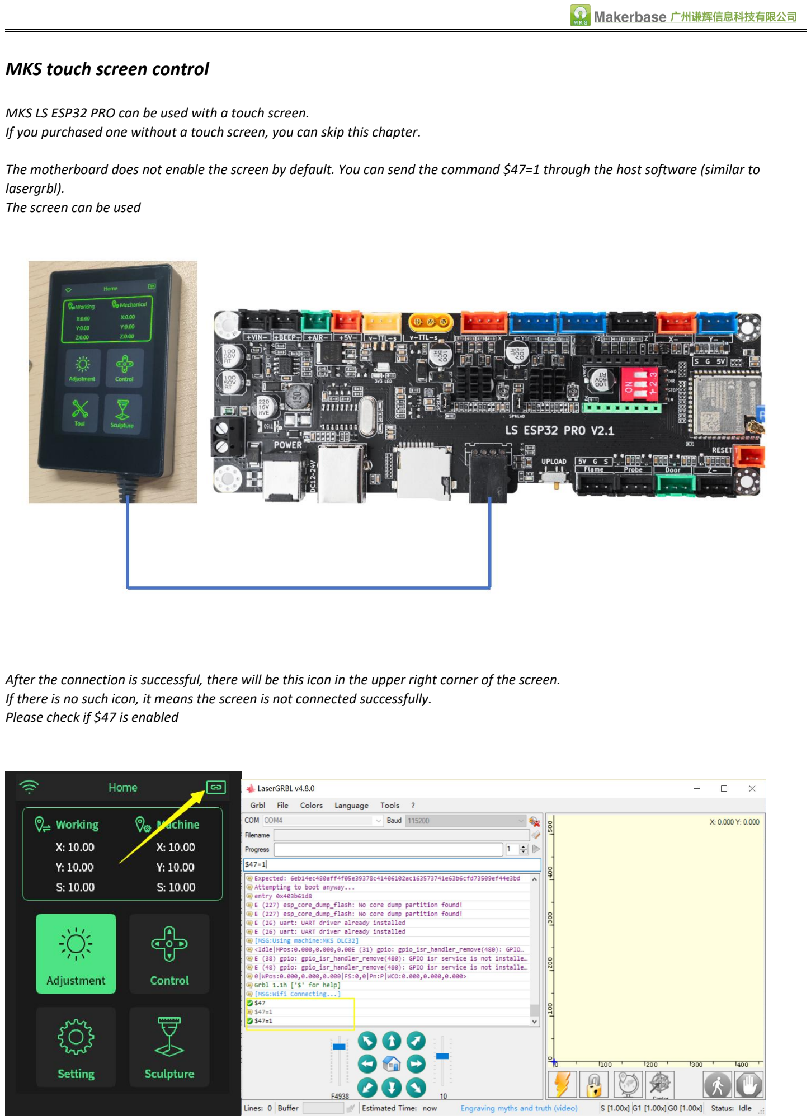
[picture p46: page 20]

MKS LS ESP32 PRO can be used with a touch screen.
If you purchased one without a touch screen, you can skip this chapter. The motherboard does not enable the screen by default. You can send the command $47=1 through the host software (similar to

lasergrbl). The screen can be used

After the connection is successful, there will be this icon in the upper right corner of the screen. If there is no such icon, it means the screen is not connected successfully. Please check if $47 is enabled

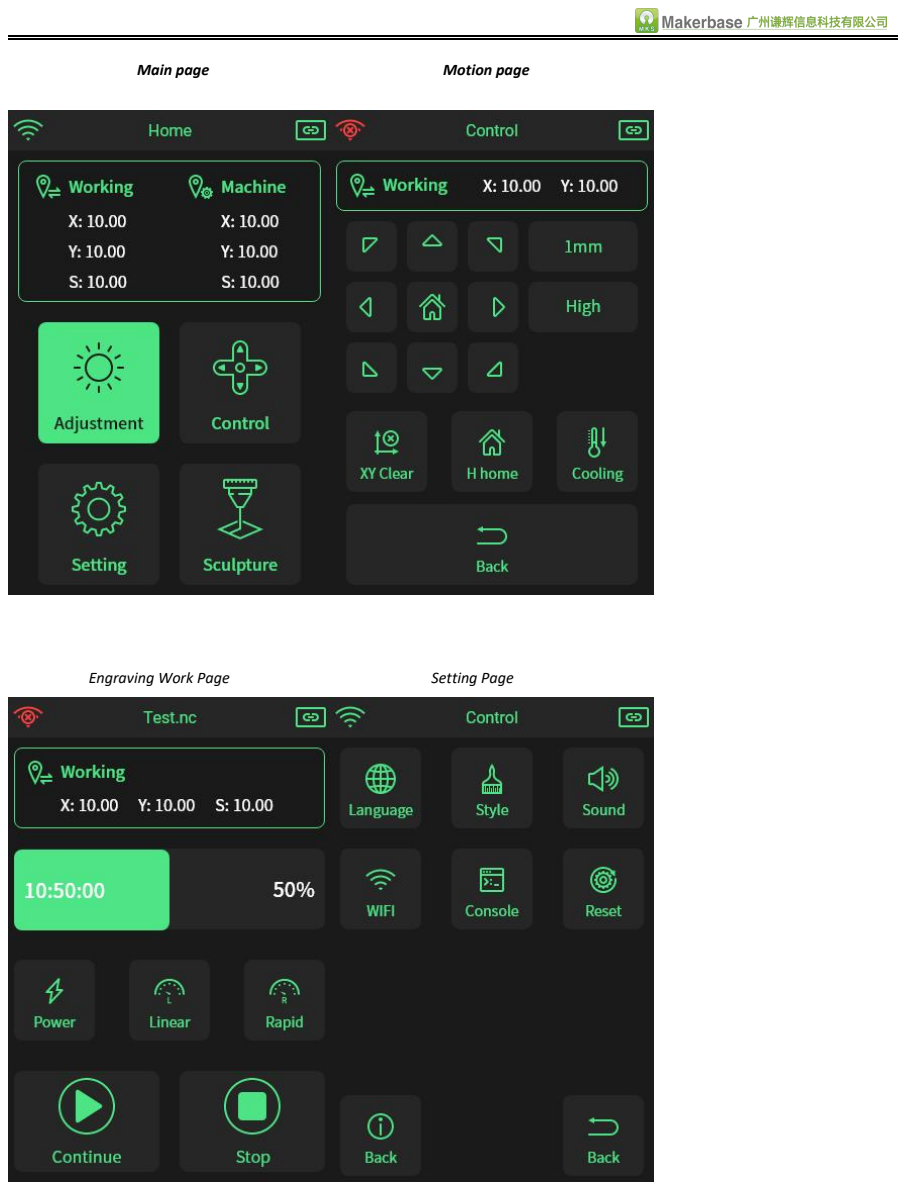
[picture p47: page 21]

Main page | Motion page
Engraving Work Page | Setting Page

If the motherboard has STA mode turned on, you can directly select the corresponding network on the screen and enter the password to connect. (If the display is empty, check the motherboard settings.)

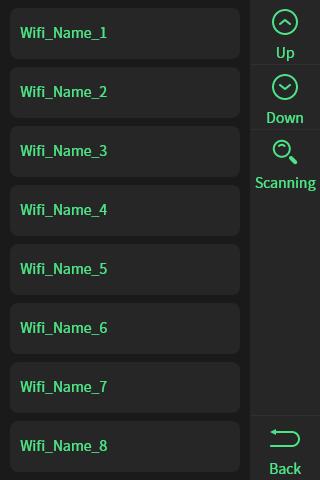
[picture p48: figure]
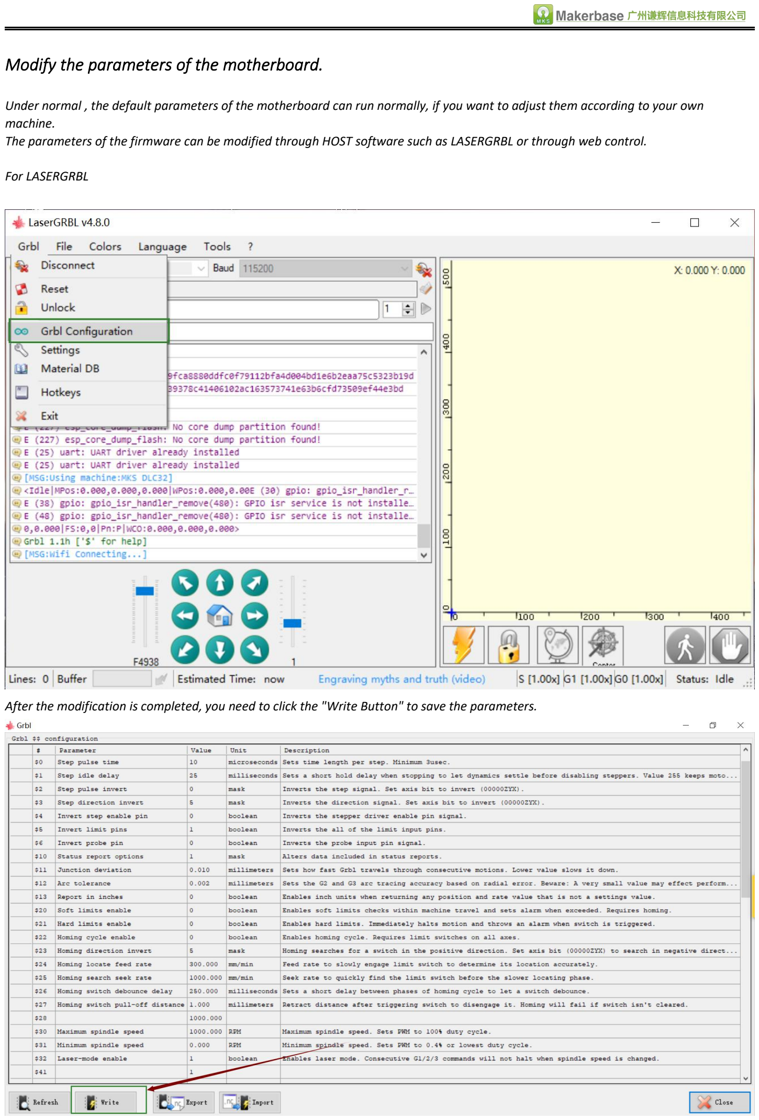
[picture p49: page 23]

Modify the parameters of the motherboard. Under normal , the default parameters of the motherboard can run normally, if you want to adjust them according to your own

machine. The parameters of the firmware can be modified through HOST software such as LASERGRBL or through web control. For LASERGRBL

After the modification is completed, you need to click the "Write Button" to save the parameters.

For Web control page

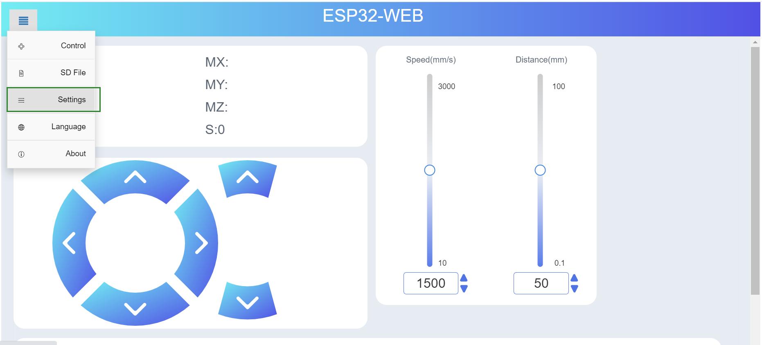
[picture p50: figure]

Modify according to the actual situation. After the modification is completed, you need to click "set" in front of the command to save the parameters.

$3 in the firmware parameters (setting the motor direction) is a parameter that sets the xyz direction. You can refer to the list below. (In fact, it is to convert the set decimal value into a binary value)

For example:
The default setting is $3=0, (x+,y+z+)
If I update to the machine, find that the directions of x and y are opposite, so your correct direction should be (x-, y-, z+). So if you look it up in the table, the corresponding direction is 3. So settings $3=3, then save, so that the motor becomes the reverse direction you want.

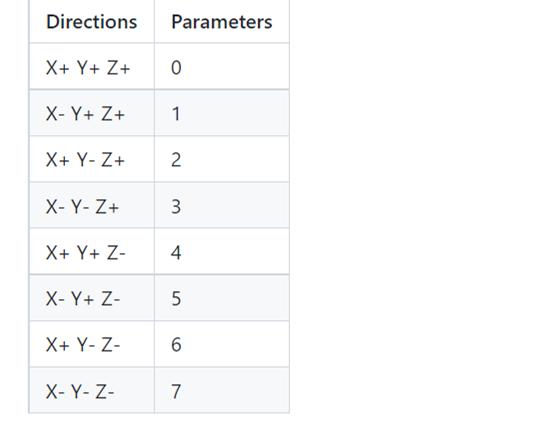
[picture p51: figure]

The following table is a special function command, which is not displayed in the parameters of Lasergrbl or web page by default. If you need to use these functions, you can refer to the instructions in the table and send commands in lasergrbl similar to the host
software to enable or disable them. $40 | 0 | Motherboard controllable 5v interface 0:disable | 1:enable
$41 | 1 | Buzzer settings 0:disable 1:enable
$42 | 0 | Probe(Tilt detection) 0:disable 1:enable(High sensitivity) 2:enable(Low sensitivity)
$43 | 0 | Flame detection setting 0:disable 1:enable(High sensitivity) 2:enable(Low sensitivity)
$44 | 0 | Air Assist 0:disable 1:enable(Minimum output 0%) 2:enable(Minimum output 5%)
$45 | 0 | Motion mode setting 0: XY axis mode 1: Roller mode (the z-axis of the motherboard is defined as the rolling axis) 2：xyz axis mode
$46 | 1 | Bard rate 1:115200，2:250000
$47 | 0 | Offline Display 0：disable 1:enable
$48 | 0 | Door detection Setting 0:disable 1:enable(High sensitivity) 2:enable(Low sensitivity)
$50 | 0 | WIFI mode setting， 0:disable，1：AP Mode，2：STA Mode， 3：Bluetooth
$51 | ESP_WIFI | AP Mode SSID
$52 | 12345678 | AP Mode Password
$53 | My_SSID | STA Mode SSID
$54 | My_password | STA Mode Password
[ESP111] | | After the connection is successful, Query the IP address

The following picture uses $41 as an example
Send the command itself directly

$41 (query the current settings of the command) sending means directly setting the corresponding status. $41=0 disable buzzer

$41=1 enable buzzer

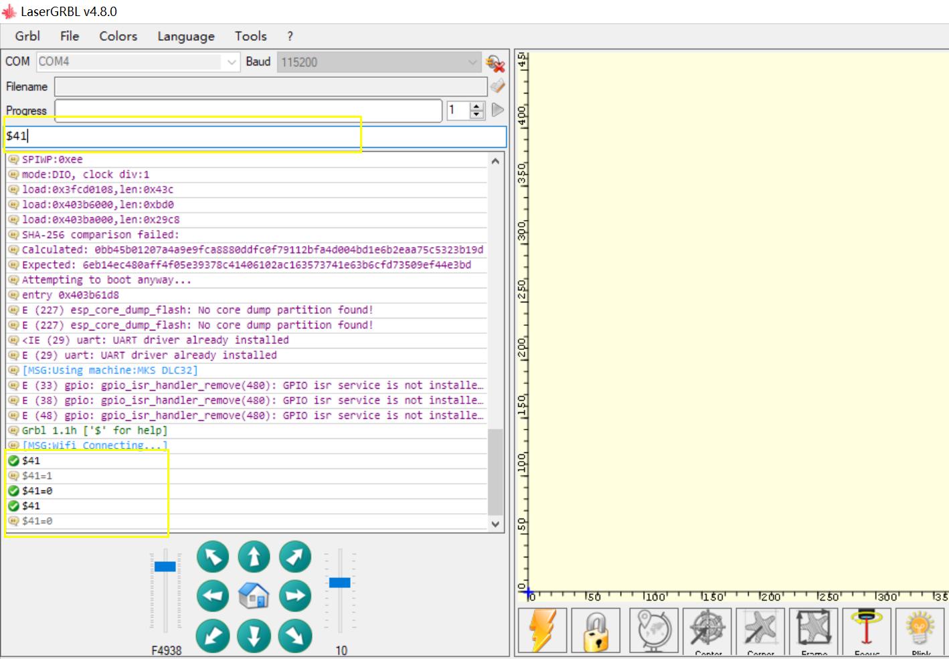
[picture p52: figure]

For this additional function (tilt detection, flame detection, door detection), they are disabled by default. If you need to use them, please enable them in advance. Note:Connecting the module, please note that the signal sequence of the motherboard interface and the signal on the module must be

connected accordingly. If the signals do not correspond, it may cause the module to not work properly. The signals of the interface are all in this order. (You can look at the silk screen on the back when connecting)

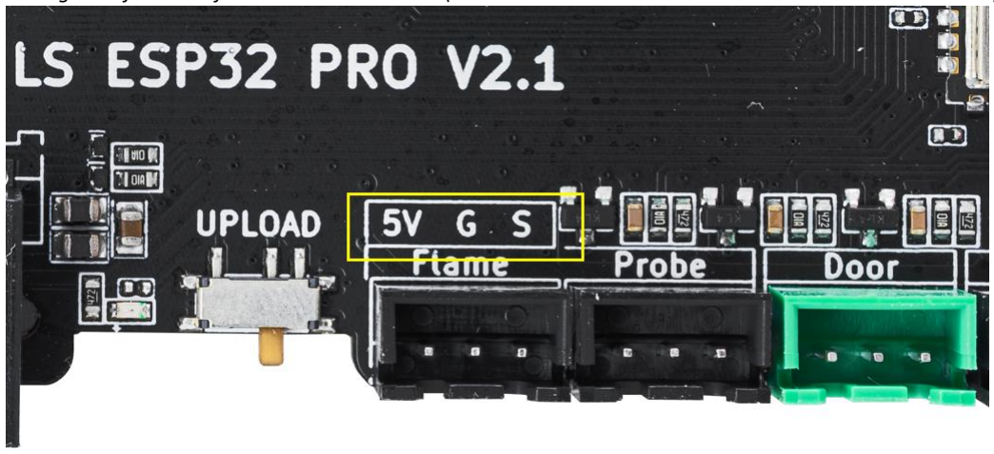
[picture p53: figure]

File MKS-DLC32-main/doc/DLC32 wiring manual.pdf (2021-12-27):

# MKS DLC32 V2 Wiring Manual

Date：2021-12-24

# Directory

## Ⅰ. Overview

MKS DLC32 is an offline engraving main control board specially developed for desktop

engraving machines.Equipped with 32-bit ESP32 module, integrated WFI function, compatible

with MKS TS2.4/3.5-inch touch screen. Supports fast engraving and web control, mobile APP

control

MKS DLC32 Interface introduction

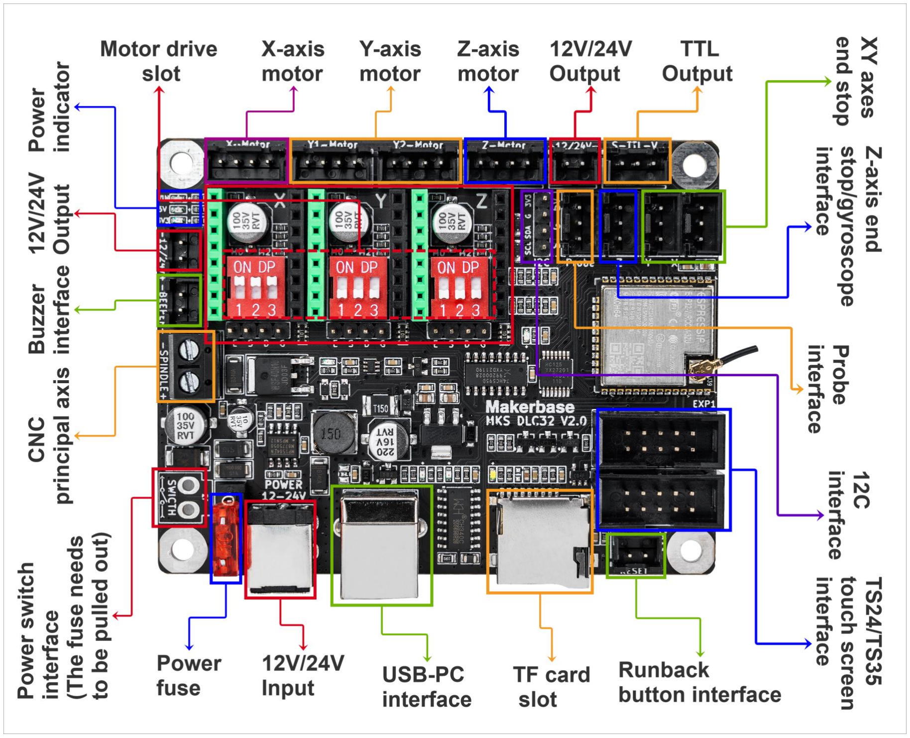
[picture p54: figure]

## Ⅱ. Power Input

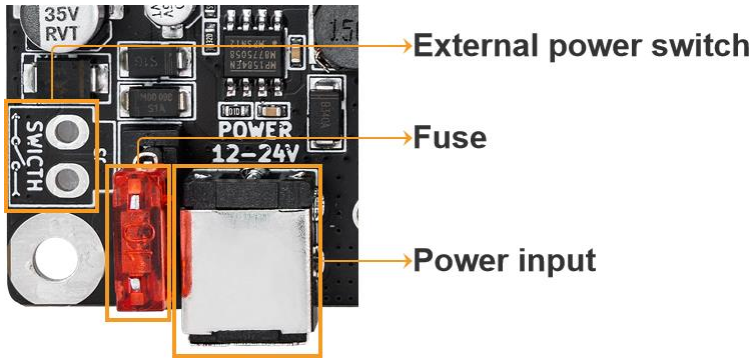
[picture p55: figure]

Power input: Voltage range 12-24V; Maximum Current 5A; Power input terminal model：

"DC-007B-2.1mm".

Fuse: 10A Fuse.

External power switch: It can be used to control the power with an external switch

Note：

1.If you need an external switch to control the power ON/OFF,Need to unplug the fuse.

2.External power switch is not a power interface, do not connect any external power

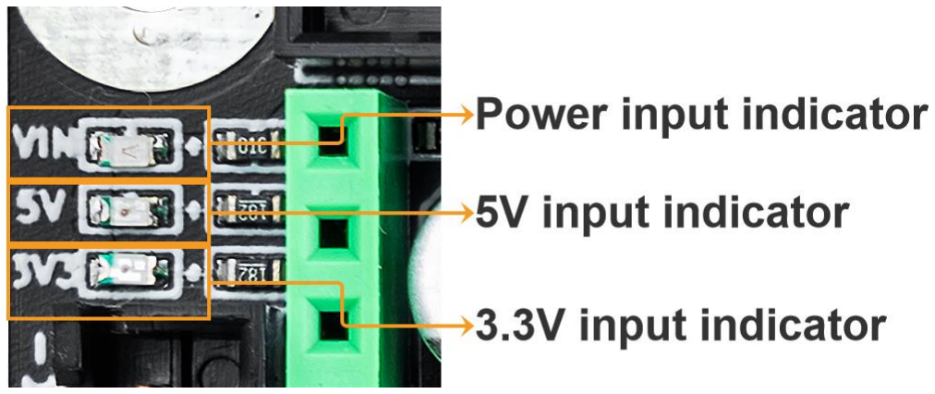
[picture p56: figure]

VIN:12V or 24V input power LED indicator. If this LED is off, please unplug the power immediately. Check

whether the 12V/24V interface on the motherboard is short-circuited, or whether the driver is plugged in reverse. The 12V/24V interface can be tested with a multimeter, and it can be powered on until it is not

short-circuited to avoid burning the circuit board.

5V:5V LED indicator. When the LED light is off, please unplug the power immediately to check whether

the endstops switch and other interfaces are short-circuited. You can check the 5V and gnd on the limit

switch with a multimeter. You can only power on it after troubleshooting. Avoid burning the circuit

board.

3.3V:3.3V LED indicator. When the LED light is off, please unplug the power immediately to check

Whether the I2C interface is short-circuited.Power on after troubleshooting

### Ⅲ. USB-PC interface

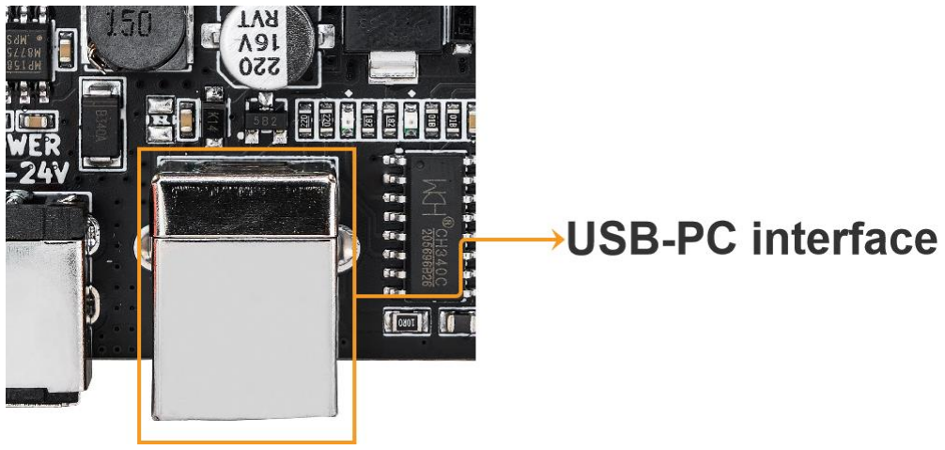
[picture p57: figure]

USB-PC interface：Used for programming and online control

NOTE:If the USB interface does not provide power supply, if you want to program or online control,

please connect to the DC power supply before you can use it. The USB serial port chip uses CH340, so

please install the CH340 driver before using it.

## Ⅳ. TF Card Slot

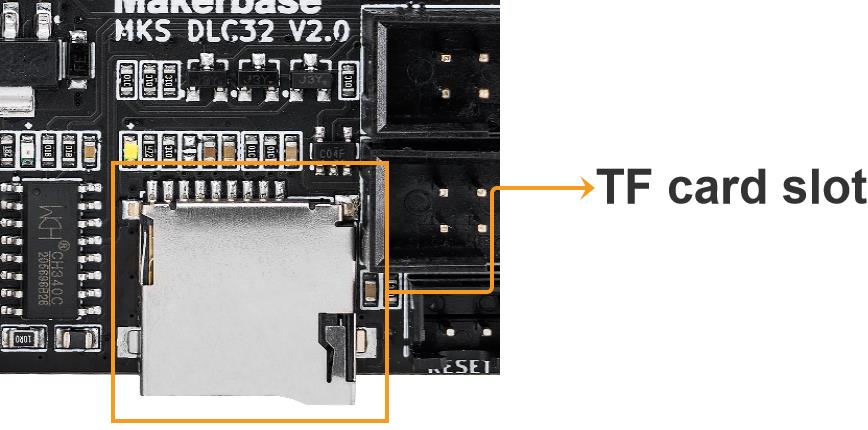
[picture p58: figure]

TF card slot: For offline engraving file storage.
Suggest SD card: Class4 or Class10; 4~16G memory; Fat32 format. File format support: .NC; .GC; .GCODE

## Ⅴ．Reset button external port (emergency stop button)

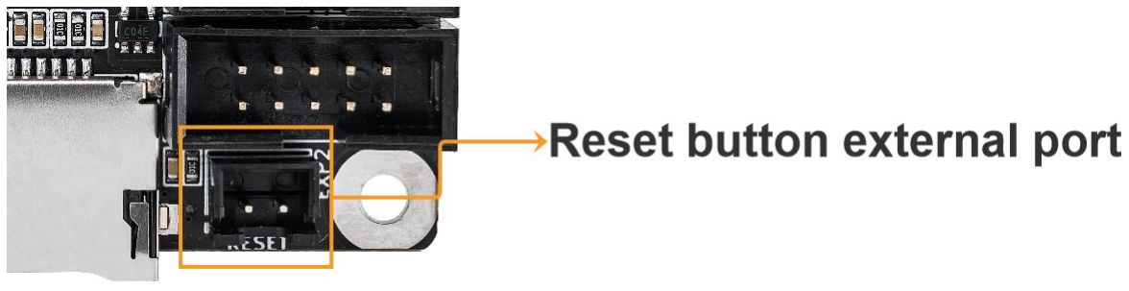
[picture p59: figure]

Reset button external port: used to reset MCU or as an emergency stop button.

## Ⅵ. Motor Drive Settings

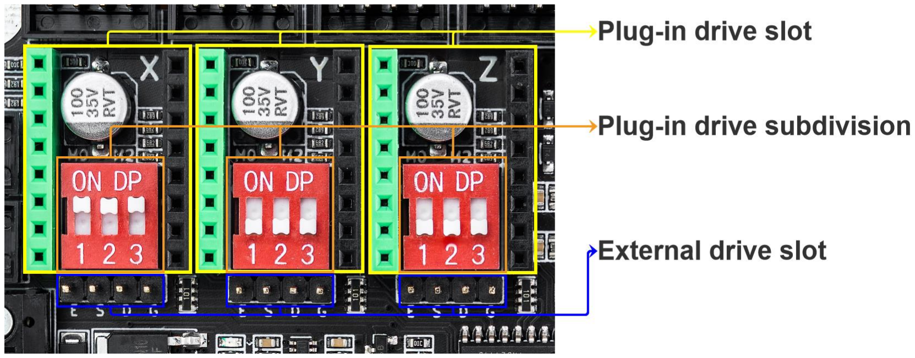
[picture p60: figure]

### 1. Plug-in drive and micro-step setting

Drive socket PINOUT

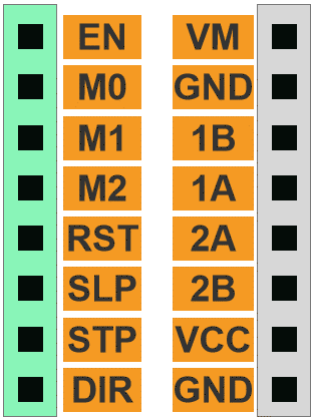
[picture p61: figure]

Micro-step setting

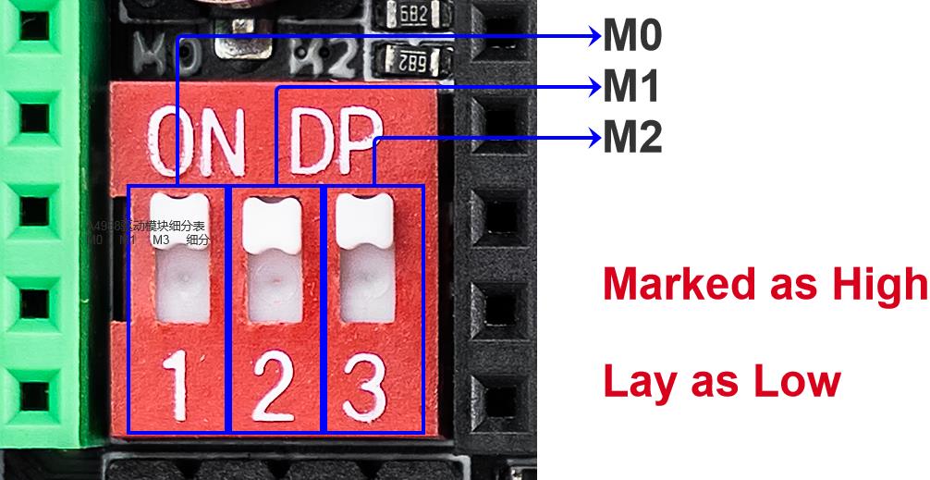
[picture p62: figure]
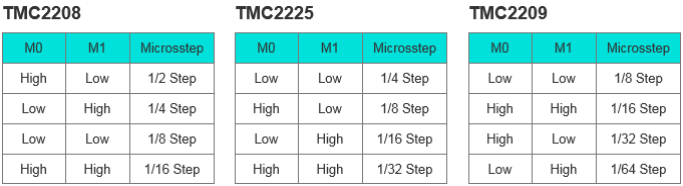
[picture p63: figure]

### 2. External high current drive connection

External drive interface:

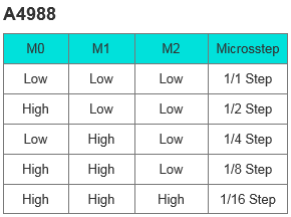
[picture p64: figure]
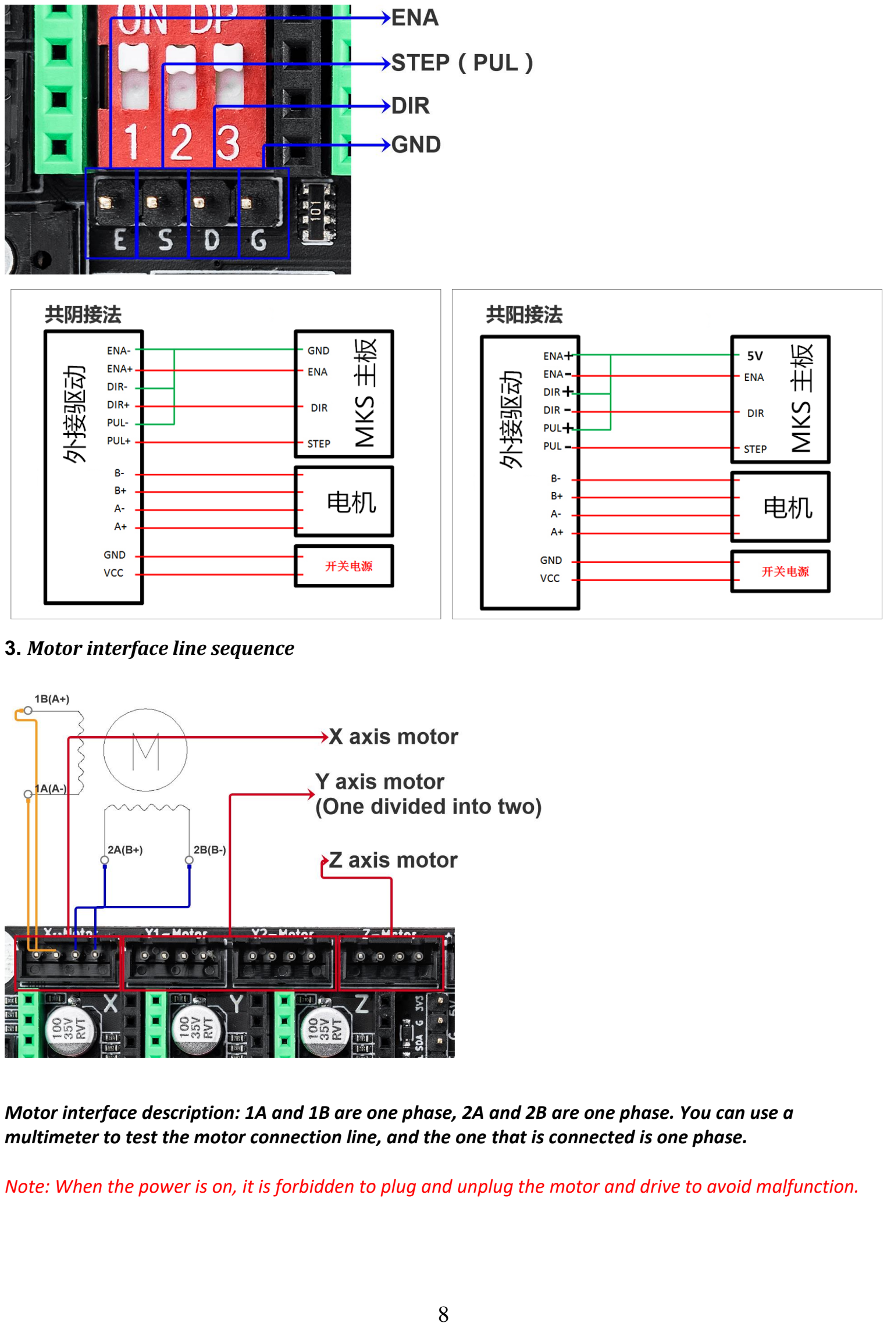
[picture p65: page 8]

### 3. Motor interface line sequence

Motor interface description: 1A and 1B are one phase, 2A and 2B are one phase. You can use a multimeter to test the motor connection line, and the one that is connected is one phase.

Note: When the power is on, it is forbidden to plug and unplug the motor and drive to avoid malfunction.

## Ⅵ . Screen interface (EXP1 and EXP2)

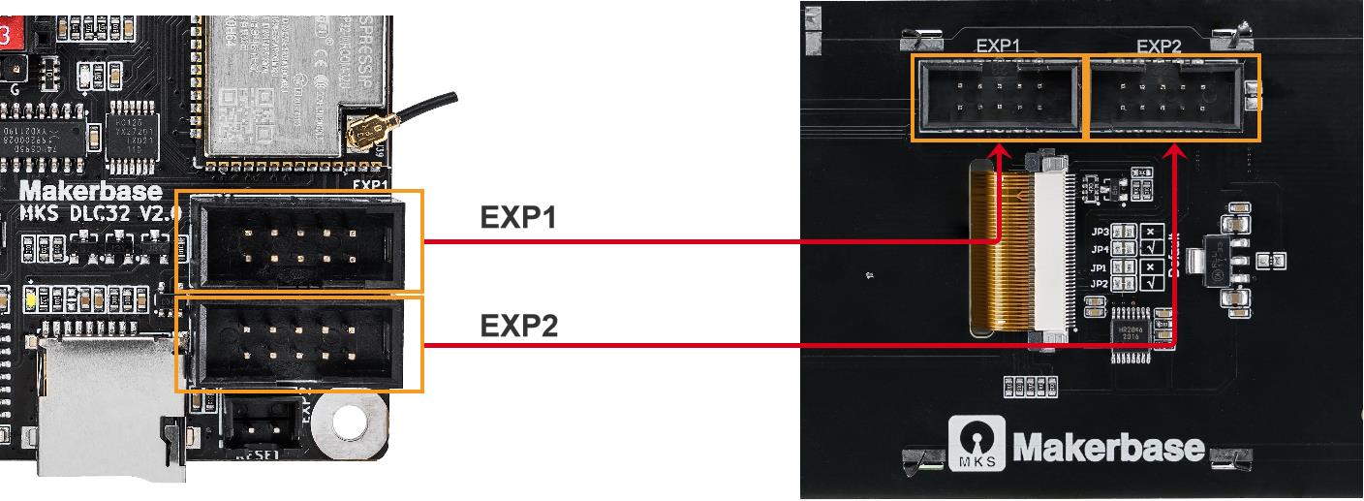
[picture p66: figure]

At present, the motherboard only supports TS35 and TS24 screens. The wiring method is as shown in the figure. The EXP1 and EXP2 of the screen correspond to the motherboard interfaces.

## Ⅶ . Laser module connection

The following shows two types of laser:
1. TTL-PWM type (3PIN). 2.12-24v-PWM(2PIN)

TTL-PWM type (3PIN)，The wiring is as follows

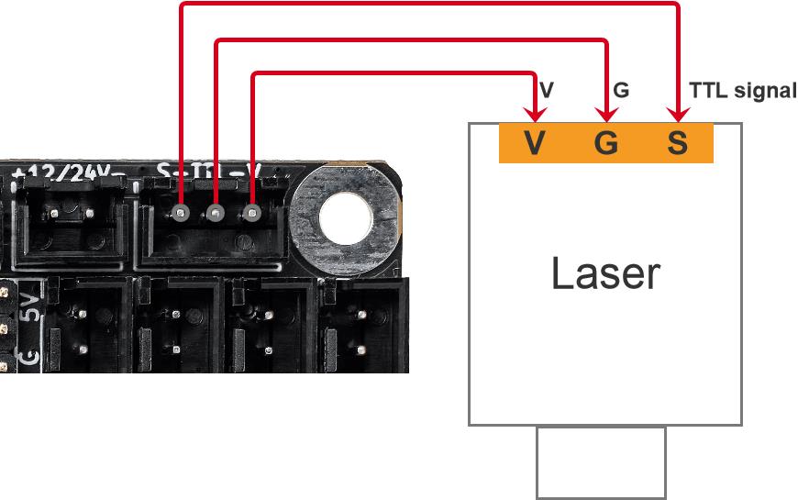
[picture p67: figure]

(V): V is the same as the power input, if the power input is 24V, then the output here is 24V. At present, the maximum power supported by the laser head is: 25W at 12V, and 50W at 24V.
(G): gnd
(TTL): TTL input is PWM, the default main frequency is 1K Hz, 1K Hz~10K Hz can be set, and the voltage is between 0V~5V.

12-24V-PWM type (2PIN)，The wiring is as follows:

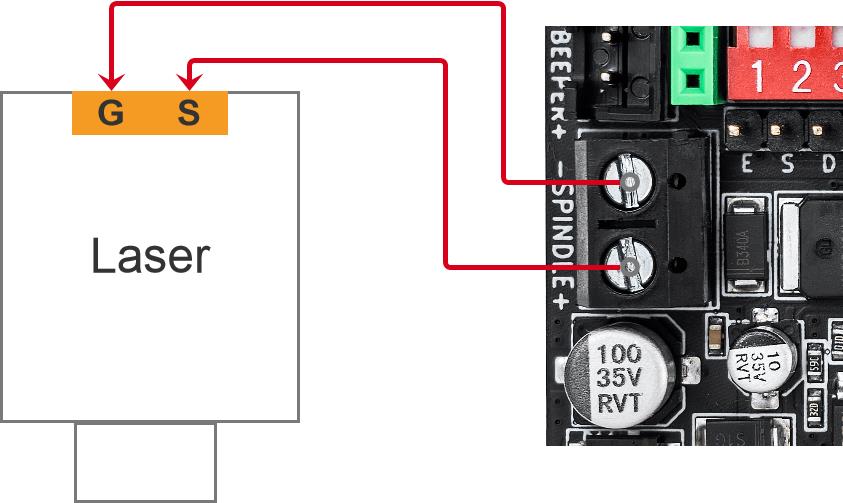
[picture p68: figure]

(S): PWM output, the signal voltage is 0V~12V or 0V~24V, the maximum voltage depends on the power input voltage. If the power supply voltage input is 24V, then the maximum output voltage of this interface is 24V. At present, the maximum power supported by the laser head is: 25W at 12V, and 50W at 24V.
(G): gnd

## Ⅷ . CNC spindle connection

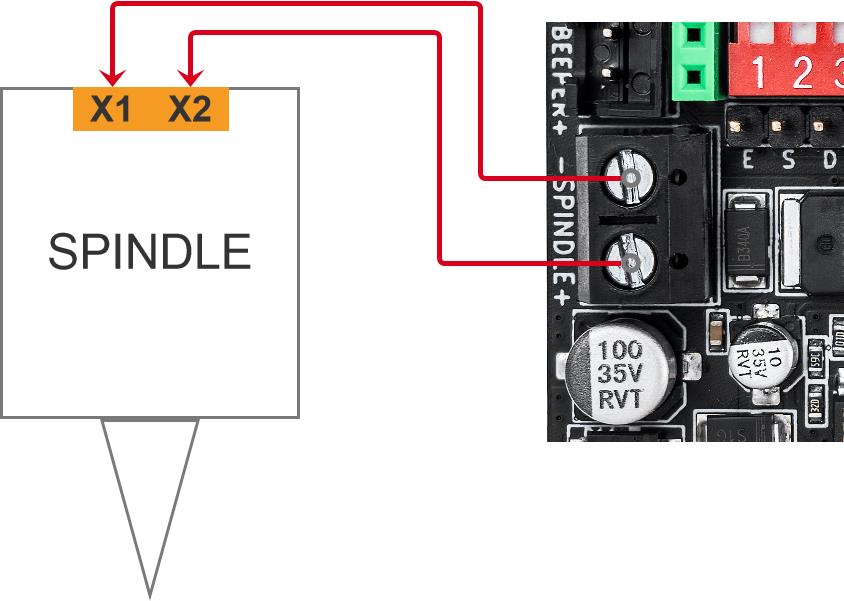
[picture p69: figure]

CNC spindle: The output voltage is 0-12V or 0-24V, and the maximum voltage depends on the voltage of the input power supply. If the input voltage of the power supply is 24V, the maximum output voltage of the SPINDLE interface is 24V. At present, the maximum power supported by the spindle motor is: 10W at 12V, and 20W at 24V.


If a higher power spindle motor requires an external module, the connection method is as shown in the figure below:

## Ⅸ . Endstop interface

X/Y/Z axis endstop switch: the limit interface of the motherboard have X/Y/Z, the input signal voltage is 5V, the signal is -S. The mechanical switch only needs GND and S, the photoelectric switch needs power supply, this interface is 5v power supply, you must confirm your switch power supply voltage.

## Ⅹ. Probe interface


Probe interface: When using CNC firmware, this interface can be used as a Probe probe. When using the laser engraving machine firmware, this interface can be used as a flame detection function.
The input signal voltage is 5V, the signal interface is S, and a 5V power supply interface is provided to supply power to the modules that need power supply.

## Ⅺ. I2C interface


I2C interface: SCL pin can be used as a cooler function output IO port.
The SDA pin can be used as firmware programming, and individual computers cannot let the motherboard enter the download mode. You can short-circuit SDA with GND and then power on to force it to enter the download mode. After downloading, please remove the short circuit and power on again to work normally.

## Ⅻ . Buzzer interface


Buzzer interface: This interface is shared with the buzzer on the screen. The current main function is to act as a reminder when an alarm is triggered (such as after the flame detection is triggered).

## ⅰ . Technical Support and Guarantee

1. Power test will be done prior to shipment to ensure normal use of the product

2. Welcome to join the discussion group in github or facebook
3. Welcome to the blog exchange: GITHUB:https://github.com/makerbase-mks/MKS-DLC32
4. 3D printer motherboard ： AliExpress:https://www.aliexpress.com/store/1047297
5. If you have any questions you can contact our customer service or find technical
support staff in the group, we will be happy to serve you.

FACEBOOK:https://www.facebook.com/Makerbase.mks/GITHUB:https://github.com/makerbase-mks/MKS-DLC32AliExpress:https://www.aliexpress.com/store/1047297

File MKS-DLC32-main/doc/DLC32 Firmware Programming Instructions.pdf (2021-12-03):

1

## DLC32 firmware programming instructions-V1.0

The purpose of this document is to explain that the process for customers to update the firmware of the DLC32 motherboard is simpler and easier to understand

## Software Installation

1.Install “MKSlaserTool-setup V1.x.x”


2

### 2. Install CH340 driver file (if your PC has already been installed, please skip this

link)

NOTE:If the PC has not installed ch340, the motherboard connected to the PC cannot be recognized and connected to DLC32

## Software programming operation process


3

### 1. Open the MKS LASER TOOL software and connect DLC32 to the PC

### 2. Set DLC32 parameters


4

Parameter setting
SPI SPEED: 80MHZ
FLASH SIZE: 8MB
Baud rate: 115200

Serial port (COM): This assigns the com of the motherboard according to the PC. This is after the CH340 driver file is installed in the previous step, the motherboard will be allocated. The motherboard in the picture is assigned “COM15”. If you don’t know the serial number, you can check it in the device manager. (Note: The serial number is not fixed, if you connect to another PC, this may change)

### 3. Select DLC32 motherboard firmware to update

5


The process is shown in the picture above. When the software shows that the update is successful, you only need to unplug the USB cable and power on again. NOTE:FAQ about the bin file used for DLC32 firmware update

Q1:Where can I download the firmware?
A1:You can go to our MKS github to download. (https://github.com/makerbase-mks/MKS-DLC32/tree/main/firmware)

Q2:Which firmware is suitable for my machine?
A2:According to your DLC32 package . TS24 SUIT or TS35 SUIT (if you buy a single motherboard, you can choose at will). Then select the corresponding function (cnc or laser), after finding the

corresponding file, download the update

If there is any problem during use. You can leave a message on our github or facebook.

FACEBOOK:https://www.facebook.com/Makerbase.mks/GITHUB:https://github.com/makerbase-mks/MKS-DLC32AliExpress:https://www.aliexpress.com/store/1047297

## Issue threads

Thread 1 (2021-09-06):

Homing does not work on 2 axis machine with hard limits

Poppy45, 2021-09-06:
homing does not work on 2 axis machine with hard limits .so need to modify firmware to stop x axis homing as per grbl instructions'.

mks-viva, 2021-09-07:
Please provide a video when your manchie homing.

Poppy45, 2021-09-07:
https://user-images.githubusercontent.com/64296414/132287709-65737b8e-4093-4b42-bb63-c7bf4416c18f.mp4

https://user-images.githubusercontent.com/64296414/132287731-7ec0ba69-0673-497d-9a13-53f34aea8c7f.mp4

goes into alarm 8 as tries to home z axis but does not exist

Poppy45, 2021-09-07:
closed by mistake

Poppy45, 2021-09-07:
as per link https://github.com/gnea/grbl/wiki/Two-Axis-System-Considerations

solawc, 2021-09-07:
> as per link https://github.com/gnea/grbl/wiki/Two-Axis-System-Considerations

Hello, although dlc32 supports the instructions and upper computer of grbl, some operations have been changed. For dlc32 just delivered, Z-axis and z-limit are not used in the firmware, so they will not start the effect. Please check whether the level setting of a lower limit bit is correct

Poppy45, 2021-09-07:
[DLC32 setting.txt](https://github.com/makerbase-mks/MKS-DLC32/files/7120574/DLC32.setting.txt)
Thanks that was i was asking. Please explain what you mean by  level setting of a lower limit bit is correct. attached is my setting in txt file

Poppy45, 2021-09-25:
got it working using NC switches need to have $5=0 not 1 which is reverse of grbl setting

Poppy45, 2021-09-25:
thanks for non help

Poppy45, 2021-09-28:
read the solution above $5=0 with NC switches not as per grbl instructions which states $5=1

Closed 2021-09-25.

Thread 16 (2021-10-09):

Manual movements over LCD very fast

trashypopashy, 2021-10-09:
My CNC-machine has all the axles driven by leadscrew. So I have to configure the steps/mm to 800. When I do this, the manual movements on the LCD-Screen are extremely fast. It is only possible to move with low setting on the LCD-menu. Moving with high or mid, my CNC tries to drive way too fast and is loosing most of the movements steps. The homing-speeds which are configured in dlc_cfg.txt do not influence these manual movements in the LCD-menu.

Could you please make a dependency between these speeds an the steps/mm? Maybe it is just the accelleration that is too high, but even the max accelleration in dlc_cfg.txt does not affect these moves.

solawc, 2021-10-14:
> The movements which I type in a gCode-File or in the console are done correctly. But the moves that are done with the control-panel on the LCD are VERY FAST (in "Low Speed" it is already fast, but my CNC can handle it), when I set the steps/mm from 80 to 800 (which I need for my leadsrewcs).

If you can upload a control video, I can better understand the phenomenon; I don't have a good concept of the speed I say to you, because I set a fixed value

trashypopashy, 2021-10-15:
I would prefer something in between... maybe the feedrates for manual moves on the LCD can be influenced in the $yx-settings in the dlc_cfg.txt.

solawc, 2021-11-25:
> @solawc Do You have an idea, how to solve this problem?

The moving speed is a fixed speed in the firmware, and the pulse setting has nothing to do with this speed. In terms of configuration, low speed is 500, medium speed is 1000, and high speed is 2000

Plottmania, 2021-11-26:
No matter how you do it but with 17 steppers and these spindles the maximum speed is around 1300 mm / min
I have tried a lot but 2000 mm / min is absolutely too fast.
I know the problem and has also the 3018 and Co.

They can't set speed records...and I would have set 1000 mm / min as the maximum speed.
A fast controller does not make a fast machine : )

trashypopashy, 2021-11-26:
> > @solawc Do You have an idea, how to solve this problem?
>
> The moving speed is a fixed speed in the firmware, and the pulse setting has nothing to do with this speed. In terms of configuration, low speed is 500, medium speed is 1000, and high speed is 2000

Could you please make half the speeds for me? So I need a CNC normal firmware with half the LCD-moved speeds fir a V1.1-Biard.

Plottmania, 2021-11-26:
You can set this yourself.

$110=1000.000
$111=1000.000
$112=200.000

No need to change the firmware!

trashypopashy, 2021-11-26:
No, this doesn't change it for the LCD-input movements.

trashypopashy, 2021-11-28:
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

@solawc please make a special firmware for me... or go open source.

trashypopashy, 2021-12-05:
> > Could you please make half the speeds for me? So I need a CNC normal firmware with half the LCD-moved speeds for a V1.1-Board.
>
> @solawc please make a special firmware for me... or go open source.

@solawc @makerbase-mks @mks-viva @MS1987 when can I get an update? And please go open source!

makerbase-mks, 2021-12-06:
@trashypopashy Would update to you today.

makerbase-mks, 2021-12-06:
[V2.0.4_H35_S_20211206_N_CNC.bin.zip](https://github.com/makerbase-mks/MKS-DLC32/files/7658589/V2.0.4_H35_S_20211206_N_CNC.bin.zip)
Please check it.

trashypopashy, 2021-12-06:
@makerbase-mks is this with
Fix the problem that $1=255 cannot be locked

Fix the problem that after some pop-up windows appear, they can't pop up in the follow-up

Fix the problem of Z zero return error

Fix the problem that the default value is not restored when re-sculpting after adjusting FeedOverride/SpindleSpeedOverride during engraving
Fix automatic WiFi reconnect
?

Which Board version is it for (V1 or V2)?

trashypopashy, 2021-12-08:
So You halfed the LCD-Speeds. Fine, but WiFi-reconnect still does not work.

trashypopashy, 2021-12-13:
@makerbase-mks or @solawc could You please give me a halfed-LCD-speed-Version if the MKS-DLC32/firmware/TS35/CNC/Normal/Board_V1.0/V2.0.7_H35_20211213_N_CNC.bin?

solawc, 2021-12-14:
> So You halfed the LCD-Speeds. Fine, but WiFi-reconnect still does not work.

Did you mean that the wifi automatic connection does not work?

solawc, 2021-12-14:
> @makerbase-mks or @solawc could You please give me a halfed-LCD-speed-Version if the MKS-DLC32/firmware/TS35/CNC/Normal/Board_V1.0/V2.0.7_H35_20211213_N_CNC.bin?

Yes, but I’m a bit busy today. I will configure a special CNC firmware for you tomorrow to reduce the speed of the screen control movement. Is it the same as the previous one?

trashypopashy, 2021-12-14:
> > So You halfed the LCD-Speeds. Fine, but WiFi-reconnect still does not work.
>
> Did you mean that the wifi automatic connection does not work?
Yes, this did not work.

trashypopashy, 2021-12-14:
> > @makerbase-mks or @solawc could You please give me a halfed-LCD-speed-Version if the MKS-DLC32/firmware/TS35/CNC/Normal/Board_V1.0/V2.0.7_H35_20211213_N_CNC.bin?
>
> Yes, but I’m a bit busy today. I will configure a special CNC firmware for you tomorrow to reduce the speed of the screen control movement. Is it the same as the previous one?

TS35, CNC, Normal, Board V1.0, halfed-LCD-speed-Version

trashypopashy, 2021-12-15:
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

I hope, You did not forget me @solawc

solawc, 2021-12-17:
[V2.0.7_H35_20211217_N_CNC_S.zip](https://github.com/makerbase-mks/MKS-DLC32/files/7731503/V2.0.7_H35_20211217_N_CNC_S.zip)
@trashypopashy

solawc, 2021-12-17:
Sorry, I was a little busy these two days, but I didn’t forget @trashypopashy

trashypopashy, 2021-12-26:
> [V2.0.4_H35_S_20211206_N_CNC.bin.zip](https://github.com/makerbase-mks/MKS-DLC32/files/7658589/V2.0.4_H35_S_20211206_N_CNC.bin.zip) Please check it.

> [V2.0.7_H35_20211217_N_CNC_S.zip](https://github.com/makerbase-mks/MKS-DLC32/files/7731503/V2.0.7_H35_20211217_N_CNC_S.zip) @trashypopashy

@solawc automatic WiFi-reconnect works now with firmware V2.0.7 on my V1-Board, BUT again the dlc_cfg.txt-uplads fails (as here: [)](https://github.com/makerbase-mks/MKS-DLC32/issues/35)

trashypopashy, 2021-12-26:
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

@solawc Even with Your lastest firmware V2.0.8 it is not possible to update the configuration with the dlc_cfg.txt

trashypopashy, 2022-01-11:
@mks-viva @MS1987 @makerbase-mks @solawc could you please help me? Maybe you can again provide a special version of the latest firmware for CNC normal with 35TFT Board V1 an halved LCD-speeds, bit this time updateable with the config-file over sd-card.

trashypopashy, 2022-01-25:
@abinoer could You please take care of a firmware with my wishes above (latest firmware for CNC normal with 35TFT Board V1 an halved LCD-speeds)?

makerbase-mks, 2022-11-15:
Code open source late but finally here: https://github.com/makerbase-mks/MKS-DLC32-FIRMWARE

Closed 2022-11-15.

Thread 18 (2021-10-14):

no Z axis movement and unable to upload firmware

grumpyduck300, 2021-10-14:
controller will not move z axis on my machine and i keep getting a sync error when using the download tool. what can i do to fix this issue?

solawc, 2021-10-14:
> controller will not move z axis on my machine and i keep getting a sync error when using the download tool. what can i do to fix this issue?

Yes, for the current firmware, since the limit return mode is not configured, the return mode is x, y return to zero, and there is no Z, so the Z axis is shielded temporarily. This will be issued and the return configuration mode will be provided at the next function version update; If there is a problem with your download, please provide feedback error information so that I can evaluate the problem

derFrickler, 2021-10-14:
Try with a lower baud rate, hat problems flashing mine with 921600 as well.

grumpyduck300, 2021-10-14:
Tried the lower baudrate same issue if there any jumpers on the board that need to be adjusted to put the board into download mode?

killrob, 2021-10-18:
>
>
> I've had the same issue. I solved my problem like this: I needed not just to start the flashing tool with admin rights, but first change the files properties >> Security >> to "full control"

i still have full control on both files, the firmware and the .exe, and i ran it as admin but still same issue than @grumpyduck300 .
the only difference is that i run a newer version of the tool the 3.9.0

rlinta, 2021-10-20:
I have a similar problem. the firmware does not load - sync error.

ch0 - io0 (esp32 pin 25)
ch1 - reset (esp32 pin 3)
ch2 - probe/io2 (esp32 pin 24)

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

killrob, 2021-10-20:
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

hi @rlinta , where do you found  the MKS ESP32 download tool?

Lazarus-Rising, 2021-11-12:
so is this the definitive answer then to the lack of movement on the Z axis?
I've uploaded the cnc firmware but still no Z axis movement.
can MKS confirm the connecting the capacitor to gnd etc is correct and will Z axis movement then be enabled in laser mode?

Anderson8153, 2021-11-16:
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

Defina BAUD: 115200 e @=0
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

makerbase-mks, 2021-11-25:
@grumpyduck300 , the latest firmware has enabled the Z axis: https://github.com/makerbase-mks/MKS-DLC32/tree/main/firmware/TS35/CNC/Normal.

For upload problem, please refer to [#19](https://github.com/makerbase-mks/MKS-DLC32/issues/19#issuecomment-978785658)

makerbase-mks, 2021-11-25:
Please try, I close this issue now. Please reopen it if you still have problem.

Closed 2021-11-25.

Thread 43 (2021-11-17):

Usage of "switch" on MKS-DLC32 V2.0

21mac, 2021-11-17:
Hi,
I wondered what the usage of the "switch" pins is. They are labelled as "J3" and there is this diagram in the documents:
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

So basically I can solder a switch to these pins to bypass the zener diode, correct?
What would be the purpose of doing so?

solawc, 2021-11-18:
> Hi, I wondered what the usage of the "switch" pins is. They are labelled as "J3" and there is this diagram in the documents: 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
>
> So basically I can solder a switch to these pins to bypass the zener diode, correct? What would be the purpose of doing so?

This position is convenient for users to use external switches to control whether their machines need to be powered on or off. As you said, you can bypass the diode externally

21mac, 2021-11-18:
Thanks for your reply.
First of all: I mistook the symbol, it's not a zener diode but a "polyfuse" (the plug-in-fuse on the board).

But bypassing it would not turn the board on or off.
When I plug the round connector into the socket, then the board instantly turns on, but the switch (which is not soldered onto the board yet) is "normally open".
So what would happen if I closed the switch? Nothing. the board IS ALREADY on and it would stay on.

The only way of using a switch that I can imagine: Removing the fuse, so that there is no other way to travel the circuit but through the switch.
But then I won't have a fuse on the board and I had to solder one into series with my switch?!
And I don't want to push 12 volts and several amps through a switch that I touch.

I am no specialist in electronis but I thought I could read the schematic/diagram correctly.
The image I posted earlier does not make any sense to me.

makerbase-mks, 2021-11-19:
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

@21mac , Yes, you are right, the way of using a switch is to  remove the fuse, and you should choose a switch which can load the current of the hold board(Suggest larger than 5A).

21mac, 2021-11-19:
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

Thanks a lot, now I understand :)

Closed 2021-11-19.

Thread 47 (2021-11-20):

MKS DCL32 V2.0 XY HOMING

Mihalch999, 2021-11-20:
Hello! I want to customize the firmware configuration on me DLC32. Since there is no search for the home position. How to do it??

21mac, 2021-11-21:
https://github.com/makerbase-mks/MKS-DLC32/blob/main/README.md#parameters-configuration
why don't you take a look at the documentation?
there is the command to enable it and the requirements.

Mihalch999, 2021-11-21:
> команда

There nothing helps.... I need to do next Also, since you are not using a z-axis, you will have to modify config.h and re-upload grbl to your arduino. About line 75 of the config.h you will see these two lines:

#define HOMING_CYCLE_0 (1<<Z_AXIS)
#define HOMING_CYCLE_1 ((1<<X_AXIS)|(1<<Y_AXIS))

You will need to change them to get homing to work without a z-axis. I'm thinking replacing the two lines with this one should work:

#define HOMING_CYCLE_0 ((1<<X_AXIS)|(1<<Y_AXIS))

Mihalch999, 2021-11-21:
But i need to change file config. Where can i take it? I have only DLC32_V2.0_D2.00.3_H35_公版_1108_N.bin

21mac, 2021-11-21:
the firmware is not open source (yet).
you cannot modify it.

you have to change the configuration via GCode + ESP-Codes.
open any software that is capable of sending GCodes manually (like laserGRBL) and send the commands from this documentation:
https://github.com/bdring/Grbl_Esp32/wiki/Settings
like
$Homing/Cycle0=X
$Homing/Cycle1=Y

Plottmania, 2021-11-21:
What a nonsense!
This is set in the GRBL without changing the firmware.
Laser mode or XY mode and would be the GRBL 1.1h
Now enter in the lines:

$3= ?  <----here
$22=?  <----here
$23=?  <----here

Where please is the problem but yes...changing firmware is important for now?!
No, it's all there and just need to understand.

Mihalch999, 2021-11-21:
Thank you, we managed to solve the problem of finding a house. But now a new problem. Something happened with 5 volts. The board no longer has 5 volts, the computer does not see it. Only the VIN indicator is on on the board

Plottmania, 2021-11-21:
Hello,
unfortunately I can't help you, but this is how it looks for me:
A Sculpfun S6 - Laser with one motor per axis.
Limit switches are inductive PL08-N (4-30 volts) and they work very well!
It is a test setup because I always change and try.
My DLC32 V1.0 and the normal firmware (factory settings).
I have already shot me some drivers but the DLC has never bothered all this : )
Never plug anything when the controller is under power...very important.

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

makerbase-mks, 2021-11-25:
> Thank you, we managed to solve the problem of finding a house. But now a new problem. Something happened with 5 volts. The board no longer has 5 volts, the computer does not see it. Only the VIN indicator is on on the board

So how is the problem now? It can work at the first, but now cannot work?

Mihalch999, 2021-11-25:
> > Thank you, we managed to solve the problem of finding a house. But now a new problem. Something happened with 5 volts. The board no longer has 5 volts, the computer does not see it. Only the VIN indicator is on on the board
>
> So how is the problem now? It can work at the first, but now cannot work?

Good afternoon! Thanks, the problem is solved. The LED on the board has burned out. I replaced it, and now everything works)

makerbase-mks, 2022-11-15:
Code open source late but finally here: https://github.com/makerbase-mks/MKS-DLC32-FIRMWARE

Closed 2021-11-29.

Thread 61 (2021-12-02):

MKSLaser app

Charus-OV, 2021-12-02:
Hello. Add a font color to the app. I use a dark theme in my phone and fonts are not visible. If you use a light theme then everything is fine
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

una2012, 2021-12-06:
Can anyone help me how to connect the phone to the MKSDLC 2 board
`Waiting for connection...
ok
[VER:1.1.2021051202:]
[OPT:PHSW]
[MSG:Using machine:MKS DLC32]
[MSG:Mode=STA:SSID=Dejan:Status=Connected:IP=192.168.1.10:MAC=94-3C-C6-67-1D-2C]
ok
Starting stream
WebUI Disconnected!
[MSG:WiFi Off]
[MSG:Client Started]
[MSG:Connecting Dejan]
[MSG:Connecting.]
[MSG:Connecting..]
[MSG:Connecting...]
[MSG:Connecting....]
[MSG:Connecting.]
[MSG:Connecting..]
[MSG:Connecting...]
[MSG:Connecting....]
[MSG:Connecting.]
[MSG:Connecting..]
[MSG:Connecting...]
[MSG:Connecting....]
[MSG:Connected with 192.168.1.10]
[MSG:Start mDNS with hostname:http://grblesp.local/]
[MSG:HTTP Started]
[MSG:TELNET Started 23]
Stream completed in 0:06
$S
$Sta/SSID=Dejan
$Sta/Password=******
$Sta/IPMode=DHCP
$Sta/IP=0.0.0.0
$Sta/Gateway=0.0.0.0
$Sta/Netmask=0.0.0.0
$AP/SSID=MKS_DLC
$AP/Password=******
$AP/IP=192.168.4.1
$AP/Channel=1
$System/Hostname=grblesp
$Http/Enable=ON
$Http/Port=80
$Telnet/Enable=ON
$Telnet/Port=23
$Radio/Mode=STA
$Notification/Type=NONE
$Notification/T1=
$Notification/T2=
$Notification/TS=
$Message/Level=Info
$User/Macro0=
$User/Macro1=
$User/Macro2=
$User/Macro3=
$Homing/Cycle0=XY
$Homing/Cycle1=
$Homing/Cycle2=
$Homing/Cycle3=
$Homing/Cycle4=
$Homing/Cycle5=
$Report/StallGuard=
$Stepper/Enable/Delay=0
$Stepper/Direction/Delay=0
$Stepper/Pulse=10
$Stepper/IdleTime=25
$Stepper/StepInvert=
$Stepper/DirInvert=X
$Stepper/EnableInvert=Off
$Limits/Invert=On
$Probe/Invert=Off
$Report/Status=1
$GCode/JunctionDeviation=0.010
$GCode/ArcTolerance=0.002
$Report/Inches=Off
$Firmware/Build=
$Limits/Soft=Off
$Limits/Hard=Off
$Homing/Enable=Off
$Homing/DirInvert=X
$Homing/Squared=
$Homing/Feed=300.000
$Homing/Seek=1000.000
$Homing/Debounce=250.000
$Homing/Pulloff=1.000
$Spindle/PWM/Frequency=1000.000
$GCode/MaxS=1000.000
$GCode/MinS=0.000
$Laser/FullPower=1000
$GCode/LaserMode=On
$GCode/Line1=
$GCode/Line0=
$Spindle/Enable/Invert=Off
$Spindle/Enable/OffWithSpeed=Off
$Coolant/Delay/TurnOn=1.000
$Spindle/Delay/SpinDown=0.000
$Spindle/Delay/SpinUp=0.000
$Spindle/PWM/Invert=Off
$Spindle/PWM/Off=0.000
$Spindle/PWM/Min=0.000
$Spindle/PWM/Max=1000.000
$Spindle/Type=LASER
$flame_status=Off
$gyro_status=Off
$beep_status=Off
$Language=0
$rollerMode=On
$X/StepsPerMm=80.000
$Y/StepsPerMm=80.000
$Z/StepsPerMm=80.000
$A/StepsPerMm=100.000
$B/StepsPerMm=100.000
$C/StepsPerMm=100.000
$X/MaxRate=6000.000
$Y/MaxRate=6000.000
$Z/MaxRate=6000.000
$A/MaxRate=1000.000
$B/MaxRate=1000.000
$C/MaxRate=1000.000
$X/Acceleration=500.000
$Y/Acceleration=500.000
$Z/Acceleration=500.000
$A/Acceleration=200.000
$B/Acceleration=200.000
$C/Acceleration=200.000
$X/Home/Mpos=0.000
$Y/Home/Mpos=0.000
$Z/Home/Mpos=0.000
$A/Home/Mpos=0.000
$B/Home/Mpos=0.000
$C/Home/Mpos=0.000
$X/MaxTravel=285.000
$Y/MaxTravel=272.000
$Z/MaxTravel=80.000
$A/MaxTravel=300.000
$B/MaxTravel=300.000
$C/MaxTravel=300.000
$X/Current/Run=0.250
$Y/Current/Run=0.250
$Z/Current/Run=0.250
$A/Current/Run=0.250
$B/Current/Run=0.250
$C/Current/Run=0.250
$X/Current/Hold=0.125
$Y/Current/Hold=0.125
$Z/Current/Hold=0.125
$A/Current/Hold=0.125
$B/Current/Hold=0.125
$C/Current/Hold=0.125
$X/Microsteps=16
$Y/Microsteps=16
$Z/Microsteps=16
$A/Microsteps=16
$B/Microsteps=16
$C/Microsteps=16
$X/StallGuard=16
$Y/StallGuard=16
$Z/StallGuard=16
$A/StallGuard=16
$B/StallGuard=16
$C/StallGuard=16
$Errors/Verbose=Off
ok
WebUI connected!`

My $S file

makerbase-mks, 2021-12-14:
Have you fixed it?

una2012, 2021-12-14:
No, I still can't connect to my Android devices.

makerbase-mks, 2021-12-15:
@Charus-OV , Of cause, I have asked the app developer to fix it.

makerbase-mks, 2022-01-07:
Have fixed on the latest version on google play.

Txuxto, 2022-01-22:
Eu instalei a placa MKS DLC 32 v2.0 in 3018 cnc, porém ao ligar o spindle a mesma indica erro e perde a comunicação.
O que pode ser?

Closed 2022-01-07.

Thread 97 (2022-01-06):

Z axis limit switch not working? (2.4" lcd, laser version)

RandomHacks-Git, 2022-01-06:
Hi, I'm trying to use a limit switch for the Z axis but the board doesn't seem to react to it, no alarm is triggered.
I tried on the "Z" connector (IO34) and the "Probe" connector (IO22) without success.

I'm using an NO switch connected between GND and the IO pin (I'm using the same configuration for the X and Y axes which work fine). I also tried changing $6 but it didn't make any difference.

I have v2.0 of the board with the 2.4" LCD and the most recent laser firmware.

Help?

MKS-hosiey, 2022-01-07:
We will update the firmware soon, and the new firmware will fix the problem

solawc, 2022-01-12:
The latest firmware can be used normally, please update

RandomHacks-Git, 2022-01-12:
Works fine now, thank you.

Closed 2022-01-12.

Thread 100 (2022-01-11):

Power Module Footprint and schematic

NicNatTech, 2022-01-11:
I question whether the footprint for the motor drivers on page 7 of the wiring diagram, as well as its schematic are correct?
My first board blew the driver on socket # (Z) JUST on power up.
Please confirm

MKS-hosiey, 2022-01-12:
Did you install the driver backwards? Confirm the wiring diagram is correct

NicNatTech, 2022-01-12:
Per the Wiring Document
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
Per Standard and schematic
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
Notice difference in pins 11-14
To clarify the only board I received blew two drivers on the z port on power up with no motors connected.

If I recall it had a black x on the underneath side of the port. (I will look tonight)
I have a replacement and others boards on order. (I believe this module is leaps and bounds ahead of the competition)
Steps taken with board
1) update firmware for CNC and
2) install three motor drivers (XYZ)  (why did board only come with two drivers?
3) power on with no motors connected( Z port blew two drivers X&Y no issues).

I went looking at github documents and noticed the discrepancy.

MKS-hosiey, 2022-01-14:
The 1A ,1B and 2A and 2B ，will only lead to different direction, which will not cause burning driven.&nbsp;

---Original---
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

Closed 2022-01-16.

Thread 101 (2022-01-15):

MKS-DLC32 and Y2 Axis with TMC2209

AngleV, 2022-01-15:
Hello

Recently i bought the MKS-DLC32 v.2.1 and the TMC2209 stepper drivers.
My goal is to connect 2 stepper motors to the Y Axis but they must work opposite.
Is this possible and if yes how can i do it properly?
Also does the TMC2209 will handle the current of the 2 stepper motors on it ?

Best regards
AngleV

manuelchaves, 2022-01-15:
Hi, I use 2 motors with no problems. Other solution is use external driver driver

AngleV, 2022-01-15:
@manuelchaves so you just plugged in the motors to the ports Y- 1 and Y-2 and they work opposite ??

Watto2021, 2022-01-16:
Yes, they should, the Y1 and Y2 have the A & B coils swapped on the circuit board layout. If both motors run the same direction when you plug in, you can just swap the A & B wires on just 1 of the Y steppers to fix it.

rizwanchishti, 2022-02-11:
Anyone knows the DIP configuration having DLC32 v2.1 and TMC 2209. Mine is working with M1 low and M2 high however the speed of the steppers is extremely slow. I was better on the eleksmaker mana board

AngleV, 2022-02-21:
@rizwanchishti

Read this

https://github.com/makerbase-mks/MKS-DLC32/blob/main/doc/DLC32%20wiring%20manual.pdf

Shaileshunawane, 2023-02-28:
> Hi, I use 2 motors with no problems. Other solution is use external driver driver

how to use external drivers on this board. because it has only three points for external drivers and I want to use 4 stepper drivers( y1 and y2) so how to connect?

Shaileshunawane, 2023-02-28:
> Yes, they should, the Y1 and Y2 have the A & B coils swapped on the circuit board layout. If both motors run the same direction when you plug in, you can just swap the A & B wires on just 1 of the Y steppers to fix it.

how to use external drivers on this board. because it has only three points for external drivers and I want to use 4 stepper drivers( y1 and y2) so how to connect?

Closed 2022-02-25.

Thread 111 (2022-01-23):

MKS DLC32 resets / short circuits anytime both limit switches are reached

pjrezai, 2022-01-23:
Hi! I am a newbie, but I don't know why the board resets / short circuits anytime both limit switches are reached. Any help would be very appreciated! :) (They are Makerbot limit switches)

makerbase-mks, 2022-01-23:
Maybe you should invert the level of the endstops

pjrezai, 2022-01-23:
> Maybe you should invert the level of the endstops

Thanks for the feedback!! Unfortunately my electronics knowledge is near 0. How would I do that? Thanks!!

pjrezai, 2022-01-24:
Is there any pictures of video I could see to make sure i'm installing it correctly so it doesn't short circuit? What do you mean by inverting them?

abinoer, 2022-01-25:
@pjrezai Short circuit? I think your wires are connected backwards. If you are using a mechanical limit, do not connect the 5V on the limit interface to avoid a short circuit caused by the wrong connection

pjrezai, 2022-01-31:
> @pjrezai Short circuit? I think your wires are connected backwards. If you are using a mechanical limit, do not connect the 5V on the limit interface to avoid a short circuit caused by the wrong connection

How do I not connect the 5V? Which one is that wire? Since all of them are connected by a pin connector

pjrezai, 2022-01-31:
Here are a couple pictures
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

pjrezai, 2022-02-04:
Any help would be appreciated! :)

abinoer, 2022-02-09:
There is screen printing on the motherboard, the red line on your picture is connected to 5V, you can pick out the red line

Closed 2022-03-16.

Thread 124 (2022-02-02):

Z axis steper driver is HOT

koszokradziej, 2022-02-02:
I have problem with Z axis in my laser. Motor doesn't move and the steper driver is very hot eaven if the motor is unplug. I replaced the steper driver with a another one but the problem is the same (steper driver is OK). So i think the problem is in the motherboard.

Can you help me?

torenich, 2022-02-03:
You might want to check the current setting on your drivers. It sounds like it is set to high.

koszokradziej, 2022-02-03:
Every driver set on the same value (0,7V on resistor) but problem are only with z axis

makerbase-mks, 2022-02-05:
@koszokradziej Can you provide a image of your connection of the board?

solawc, 2022-02-08:
@koszokradziej After you connect the Z axis, is the Z axis always in a locked state? And when the X/Y axis is unlocked, is it still locked?

koszokradziej, 2022-02-08:
@solawc Yes

abinoer, 2023-01-09:
Try to change to a good motor drive, if there is still this problem, there may be hardware damage

Closed 2023-01-09.

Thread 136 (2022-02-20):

More Information on the MKS DLC32 v2

Hargard339, 2022-02-20:
Hi. Its the V2 board that I can find only very little information online regarding this board.
Yes its quite a new board.
What I have found is :- https://github.com/makerbase-mks/MKS-DLC32/blob/main/doc/DLC32%20wiring%20manual.pdf
https://github.com/makerbase-mks/MKS-DLC32/blob/main/doc/DLC32%20Firmware%20Programming%20Instructions.pdf
https://github.com/makerbase-mks/MKS-DLC32/wiki/Firmware
Very little on setting up drivers.. IE TMC2209 and other drivers.
There are No videos for the V2 version.
Only this one which is Not the V2 version. https://www.youtube.com/watch?v=G1q-eSL_V_I
Thanks in Advance.

Regards Hargard.

abinoer, 2022-02-21:
Do you mean the breakdown Settings for various drivers?

TheExpertNoob, 2022-02-22:
...and differences between the v2.0 and v2.1 board.

Hargard339, 2022-02-24:
Hi. Thanks. I now have my board and screen. Will use DRV8825 drivers so start with.
With no method of setting up the drivers Not sure the board is all its cracked up to be..
Start tomorrow pm sometime and just connect everything up as shown in the video for the V1 board.

abinoer, 2022-02-25:
!
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
[1645777937(1)](https://user-images.githubusercontent.com/96047125/155682168-95f0bd3c-e906-4b11-b0a8-4400677d0955.png)
@Hargard339 All dip switches are upturned. DRV8825 is 1/32 step

abinoer, 2022-02-25:
@TheExpertNoob 2.1 version compared with 2.0 version, 2.1 has gold sinking process and more detailed screen printing, there is no difference in other places

VukIgor, 2022-03-26:
Hi ,got new board via aliexpres dlc32 v2.1 with ts24 and tmc2209 ,installed firmware,runnded lightburn and hit an issue ,"feedrate is not defined " and in lasergrbl something like "run grbl on another type of board" ... in lightburn every movement was in reverse even if it shouldnt be becouse before mks board i had ramps 1,4 running without issue with grbl . There isnt any documentation for that board and it is waste of time and $60 becouse thing dont work as it should with provided laser firmware from makerbase

Hargard339, 2022-04-02:
The board on first start was not interfacing to the screen very well. Inverted and upside down. This was fixed by flashing new firmware to the board.. Easy fix.
The installation of the TMC2209 drivers... Required no setup or messing around. Basically they are plug and play with this board other than the Microstep settings.
All good with the settings.
The only thing I dislike about the board is the Power supply input that is at the front. as this spoils the enclosure panel having a plug and cable at the front of the machine. Needs one at the sides or rear of board.
A good product. But documentation could be a lot better.

Thanks... for a great product.
Hargard.

Rickrat, 2023-04-17:
Harvard, there are holes on the MB so you can solder another pigtail jack and route it out the back.

Closed 2022-04-02.

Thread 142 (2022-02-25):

Some Issues

lasermanx, 2022-02-25:
Hello,
I just setup my board for a DIY diode laser today. I am having some issues.

The movement of motors is not smooth ie. jittery.

Also the laser Test Fire in Lightburn turns off  the laser after 15-25 seconds.

Anybody experiencing similar issues?

abinoer, 2022-02-25:
1.  Maybe the motor wiring sequence is wrong. Please check it.
2.  The laser will turn off after more than 10 seconds because of the protection function, which is normal.

lasermanx, 2022-02-25:
1. I have checked the wiring. Engraving is perfect but movement of motor is not very smooth.
2. I want extended time for focusing of the diode. How is this possible in lightburn?

lasermanx, 2022-02-25:
Tried lasergrbl M3 S100 and the laser turns off after a few seconds. How am I supposed to focus the laser?

abinoer, 2022-02-25:
@lasermanx
1. What is the specific situation of motor unsmoothness you mentioned? Is there any video
2.  You can adjust the distance of the lens or laser head to the material, then turn on the laser to observe the focus, and adjust accordingly

lasermanx, 2022-02-25:
I am not able to upload the video here so I have sent it over Facebook.

Is there any way to disable safety because I need to focus very delicately simply measuring distance does not help.

I don’t want this safety feature. Can you tell me how to disable this. I want to manually turn off laser in Test Fire mode.

abinoer, 2022-03-03:
In fact, this will not affect the focus too much, we can only disable this protection function by changing the firmware, but our r&d personnel are very busy at present

lasermanx, 2022-03-07:
I am not able to set $33 and also M4 commands are not working. Do you think I have a bad board.

abinoer, 2022-03-09:
The $33 setting has already been deleted, probably not updated on his wiki. If you want to set the spindle pulse rate, go to $28. The M4 works, but it only seems to work while on the move.

lasermanx, 2022-03-09:
Thanks for the clarification. The Test Fire turns off sometimes after 3 seconds, 15 seconds, 18 seconds or 28 seconds. It is very random. This is normal or do I have something going wrong?

abinoer, 2022-03-10:
@lasermanx Use the M4? It only turns on when it's moving. It turns off when the motor stops. Therefore, the length of movement time determines the laser on time

Closed 2022-03-17.

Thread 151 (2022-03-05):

Laser and CNC on the same machine

serper, 2022-03-05:
https://github.com/makerbase-mks/MKS-DLC32/issues/119

A month waiting for a response to finally receive the answer "Sorry, only firmware can be replaced in this case" and close the question.

The idea is to be able to use the command M6 Tn (n = tool) to select the tool. You can use the I2C pins (two pins) and use relays, triacs, mosfets, ... according to the needs of each one.

In this firmware we have very big restrictions. All to be able to use the display, but to the answer "Sorry, only firmware can be replaced in this case" the reply is clear: OK, I change the firmware to FluidNC which does allow this and much more. I will lose the display but it is preferable.

abinoer, 2022-03-07:
Engineers thought the combination of laser and CNC would cause some problems, such as burning MOSFET, and after careful evaluation decided to continue to separate the two firmware. Sorry for the late reply

serper, 2022-03-07:
In my machine (for example) I have the laser in the connection for laser and the spindle with a relay connected to the SCL pin, the power here is external to the board. The idea is to be able to select the tool being able to configure in some way where each thing is connected. In FluidNC for example you can configure the GPIO4 as a relay where you will connect the spindle. Then with the M6 Tn command you select the tool, this allows you to combine the tool in the same job.

abinoer, 2022-03-09:
All GPIO has been used up and SCL has been used for M7/M8

Closed 2022-03-21.

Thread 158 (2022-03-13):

DLC32 with TMC2209 speed problem

Fusselbirne, 2022-03-13:
My new Controller DLC32 v.2.1 is coming with TMC2209 v2.0 driver. My small CNC 3018 with nema17 Stepper run not faster than 1400 ( gcode: G1 X100 F1400). With my old driver A4988 stepper is working up to 3000 speed. I try with 1/8 and 1/16 microsteps and vref from 0.8 up to 1.4v but nothing is working. Is V2 of this driver not compatible with that controller? What can I do to work with that driver?

abinoer, 2022-03-14:
Did you actually move the correct distance when you used 2209? Or maybe the maximum speed and acceleration are set differently,

Fusselbirne, 2022-03-14:
Yes I adjusts all grbl settings. When I move „G1 X100 F1000“ it’s moving 100mm, right. But faster than 1400 to move it’s not possible. Acceleration is 200. And with drivers A4988 it’s working faster. I have controlled the real speed with stop watch.

Ondrashek, 2022-03-14:
$100-$112 to 6000
$110-$122 to 500

Fusselbirne, 2022-03-15:
Yes it was presets, but in this case move over „G0“ all motors blocked.

abinoer, 2022-03-15:
I can't reproduce this problem. What operations did you do and then found this problem? Can you provide the video

Fusselbirne, 2022-03-15:
Sorry i can't do video, i'm not home until friday.
But again from beginning. I have CNC 3018 from china with cheap grbl controller and cheap drivers (A4988) but it works fine. Then i order better controller, dlc32, with better drivers, TMC2209, for more power, quieter and more features, it was the plan. My new toy was coming and i load cnc firmware, connect all cables and check the grbl settings. It was different but plausible, ok let's try. I write " G1 X100 F500" in Candle console and juhu my spindle is on the way. But it was really slow and travel distance not right. Ok i have to adjust the grbl parameters, no problem. Set the $100 -$102 (steps/mm) from 80 to 400 like my old settings and try again. Ok it was better but not perfect. Speed was better but travel distance was half, not 100mm only 50mm. Ok i use 1/16 microstepping it's different. Give $100=800 and try again. Now is right. Travel distance 100mm speed (f500) like the same my previous controller and more quite, wonderful. Ok now we check full speed. Write "G0 X0" and.. my CNC is crying not moving. $110 -$112 (max mm/min) was 6000 preset, ok maybe to much for my litle CNC. I change $110-$112 to 2000 and ... right it's not moving. What??? wtf is it, it's worse like my old drivers. Cross check with my A4988 on DLC32 board. And right, only the direction is wrong but its going. More then 3200 (G1 X-100 F3200) it lose same steps. But 3000 without load it's save. Then i compare A4988 vs. TMC over stopwatch with speed 1000 (G1 X100 F1000). It is the same. I check the Y-axis and it's the same sch.... The TMC can't faster then 1400. And i have no idea why.

abinoer, 2022-03-16:
I am very sorry that I have not reappeared this problem until now,My Settings are the same as yours, Max speed set to 2000, acceleration 200, and 1/16 microstepping. Can the laser be turned on when the motor is not moving? Have you tried switching to another 2209? What if 2209 was damaged

Fusselbirne, 2022-03-16:
No I  have only one set A4988 drivers and one set TMC2209. But I tried TMC drivers on my old controller board and it was same result. The new TMC2209 is “grandpa version”.

abinoer, 2022-03-25:
We tried it here, 2209 does have a lower speed limit than 4988, and 2009 does have a weaker speed

Fusselbirne, 2022-03-25:
That’s not good news, anyway. And the newer type TMC2225 what have this for speed limit. Can I move faster with type, like 4988 or is that “grandpa version” to?

abinoer, 2022-03-28:
Sorry, this is the deficiency of 2209 chip, we can not solve it. If you want to use the 2209, you have to set the speed lower.

manitoulin-maker, 2022-08-03:
what is the speed rating for the tmc2225 and can the tmc2226 be used as well? its basically just a better 2209 right?

Closed 2022-03-28.

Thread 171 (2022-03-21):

MKS DLC 32 Limit Switch connection

idilbaz, 2022-03-21:
Hello, I will connect to my mks dlc 32 board with two limit switches on each axis. Is it okay if I make the connection as in the following figure?

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

serial-tintypist, 2022-03-21:
Unfortunately, these particular switches will not work when connected in parallel like this (I know this from experience with my setup). You need to disconnect the red (5 V) line and use signal and GND only.

idilbaz, 2022-03-22:
In which way do I need to connect these shapes (A or B)
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

idilbaz, 2022-03-22:
> Unfortunately, these particular switches will not work when connected in parallel like this (I know this from experience with my setup). You need to disconnect the red (5 V) line and use signal and GND only.

In which way do I need to connect these shapes (A or B)

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

serial-tintypist, 2022-03-22:
B (green is signal and black is GND)

idilbaz, 2022-03-22:
> B (green is signal and black is GND)

Thank you so much :)

kweilim98, 2022-03-22:
I try already  with as u say but when I touch the limit switch, why it delay to respond? And after that my touch screen panel restart again problem happen, how?

idilbaz, 2022-03-25:
Hello, as you said, I made the connections as in figure B, but it does not work properly.  The Z axis limit switch does not work at all, and when the others touch the limit switch button, it gives an alarm in the UGS program, but it resets itself and starts the program again.  Why does the problem occur?  Did I make the connections wrong?

idilbaz, 2022-03-26:
My problem is solved.  The problem is with these limit switches.  They are not suitable for CNC machine.  I just used a limit switch, everything seems fine now.

kweilim98, 2022-03-29:
> My problem is solved. The problem is with these limit switches. They are not suitable for CNC machine. I just used a limit switch, everything seems fine now.

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

Bro, does u mean this limit switch module not suitable for the CNC?

idilbaz, 2022-03-29:
>

Yes my friend.  I used Arduino CNC Shield before, and these limit switches did not work.  These switches did not work on the MKS DLC 32 board either.

mikaildogru, 2023-02-18:
hey friend how did you solve this probem?. I will plan door switch to connect sEmergency switches with series type ?. What do you think

kweilim98, 2023-02-19:
> hey friend how did you solve this probem?. I will plan door switch to connect sEmergency switches with series type ?. What do you think

What kind switch you using?

levent362727, 2023-12-27:
Merhaba ben mks dlc32 v2.1 kartim icin end stop kullanıyorum cihaz yeniden başlıyor neden oluyor bide gec algılıyor neden oluyor fikiri olan varmı

Closed 2022-05-16.

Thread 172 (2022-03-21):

Request: Change Emergency Stop button behaviour

daxliniere, 2022-03-21:
Currently, the Emergency Stop button completely resets the ESP32. This results in loss of position and other data.

It would be best if this was reconfigured to pause the program.

Better still, since I'm using a locking 'mushroom-type' switch, it would be great if the program would be un-paused when the switch contacts were opened again.

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

kweilim98, 2022-03-22:
Agree with you suggest

abinoer, 2022-03-29:
I'm sorry, there is no extra IO to realize what you said

daxliniere, 2022-03-31:
Hello @abinoer, perhaps you have misunderstood my request. I'm not asking for an additional button to be added, but instead for the existing function to be re-written to pause the CNC, rather than resetting the microcontroller. Losing your positioning is a real pain, especially if you just wanted to pause the program.

As a side note, it seems that quite often it comes up that features can't be added because of a lack of available IO pins. It would be very advantageous to add 1) some extra input pins on the next version of this board and 2) support I2C-based I/O expander add-on boards.

Operater2803, 2024-12-01:
Seems old thread but Im currently serching for solution on this problem and i agree with daxliniere on this. My thinking is in way to use one of the unused IO ports like SDA pin it says that is used as cooling option port, maybe it can be programmed in firmware to be input port for E stop and just to halt operations. From my opinion this should exist for CNC firmware as not much use of cooling port here if one needs cooling just conect it together with spindle start relay. On the other side on laser firmware I used it as Air blow start during program run. Also on laser Firmware I think that probe IO22 pin is used as Fire detection and that is used to halt all operations so from my opinion can be used as E stop also. Correct me if im wrong.

Closed 2022-03-29.

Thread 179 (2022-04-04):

Limit pins invert issue

dhanninacs, 2022-04-04:
I have dual y axis stepper motors and two y limit switches on either side in Normally open position connected in series. So both switches need to trigger for hard limit to switch on. I'm using $5=1 to achieve this.

But doing this, the x-limit switch which is also connected to Normally open and ground doesn't trigger when the limit switch is pushed. I have tried other limit switches to see if it is the problem but it looks like more of an $5 issues on board side. Did anyone have similar issues? I have a DLC 32 v2.1 board.

abinoer, 2022-04-06:
I don't quite understand your description. Are you in a situation where Y-limit works and X-Limit doesn't? Is only one Y Limit Switches and one X Limit Switches restored? Can you upload wiring pictures

dhanninacs, 2022-04-06:
Hi yes, when I have $5=1, and the X-axis limit switch connected to normally open position. The limit switch doesn't trigger when pushed.

abinoer, 2022-04-06:
Short X limit interface S and GMD, can trigger? If so, there's something wrong with your limit switch

dhanninacs, 2022-04-06:
I have tried other limit switches, they too don’t work. With $5=0 and limit switches connected in normally closed position everything works fine.

dhanninacs, 2022-04-07:
It was a wiring issue. All sorted out now and works as intended. Thanks

Closed 2022-04-07.

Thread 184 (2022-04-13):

Open Source Firmware

CLP58, 2022-04-13:
You already said last October that you were ready to open source and it has been six months since then? When will you open source the firmware?
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

MTRatcliffe, 2022-05-08:
Would be nice to see this shared and to see what comes from it.

geogarden, 2022-05-26:
Promises must be kept :)

Hargard339, 2022-05-29:
Yes please To many issues for this Board. Make it open source.
It helps you and it helps Us.
Regards.

Lasermax3000, 2022-06-07:
That would be great!!!
Don´t know why MKS doesn´t want the help from the Community supporting there Board and making there Firmware better for free.
I think if the Firmware would be better and you would have more options for customizations the Board would be more atractive for people out there -> potential buyers....just saying.

pedropvbh, 2022-06-26:
it's past time to release

Hargard339, 2022-06-26:
Wake up MKS we are here to help you as well. Listen to your supporters/customers.
Open Source is the way to go.

skaterdude, 2022-07-01:
Considering buying some of these boards with displays for various projects.  Without open source software, however, it's easier to continue with my own custom breadboard.

distebia, 2022-07-07:
ho bisogno di aumentare la mia uscita minima del pwm, su arduino impostavo spindle/pwm/min a 25 e risolvevo il problema...ora sono su mks dlc32 v2.1, la macchina è la stessa quindi con il solito problema dell'alimentatore co2 che vuole aumentata l'uscita minima, e mi sento dire che i parametri $30=1000, $31=0, $35=0 sono bloccati e, anche se vario i valori, non ottengo nessun cambiamento. un conto è avere un firmware protetto e non pubblico, un conto è avere variabili del firmware che non si possono modificare...non abbiamo tutti la stessa macchina laser o cnc, ogni utente è diverso e richiede parametri specifici.

dixi83, 2022-10-02:
> Why not making the source open merging this development work with FluidNC?

Why not see if we could get FluidNC working ;) waiting for MKS is a useless case. There is a config file provided ( https://github.com/bdring/FluidNC/blob/main/example_configs/MKS_DLC32_21_XYZ.yaml ) But could net get it to work on my V2.1 with TMC2209's. Because I am still building my machine, I did not spend many time on this. I needed movement so I switched back. I will give it another try when the machine is finished.

mikerocklewitz, 2022-10-05:
Im with everyone here.  Open the source.....or at least give us a good config for both cnc and laser, with some info for using different drivers and spindle/laser options with fluidnc.

Ive had this board sitting in my drawer for over 8 months now. I wanna use it on my 3018. Ive  tried getting the provided firmware to work but was met with nothing but issues.  Then I tried getting fluidnc to work but man thats a nightmare building a config off of the xyz laser example they have for this board. Nothin but issues.

Give us the goods already! Ull sell more

skaterdude, 2022-10-05:
I gave up.  It's not worth waiting, and I've got lots of other projects to do.

Hargard339, 2022-10-06:
I have as well. Threw my MKS DLC in the junk box as the firmware is not fit for purpose.   Will NOT purchase a MKS board again without first checking that we can adapt it to our requirements.
WAKE UP MKS.

makerbase-mks, 2022-11-15:
Code open source late but finally here: https://github.com/makerbase-mks/MKS-DLC32-FIRMWARE

Closed 2022-11-15.

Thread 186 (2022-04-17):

Limit switches X + Y

bbuster2, 2022-04-17:
Which endstops can i use to detect the end of the X and Y axis?
And can i use it on both sides or is it just on one side of each axis to auto home?

I would like to limit the X,Y on the 0,0 and also X,Y

Can i also use inductive limit switches like https://www.benselectronics.nl/inductieve-proximity-sensor-npn.html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

Plottmania, 2022-04-18:
You can use this on a DLC32...no Problem : )

https://youtu.be/KuEqwmGYVGg

bbuster2, 2022-04-18:
Are you sure, the ones i posted are not the ones in the video, he uses PL-08N.
And am i also able to use 2 sensors per axis to limit to both ends of the axis?

Plottmania, 2022-04-19:
Why, I use there in theVideo inductive limit switches for a reference run.
I do not need limit switches at the end of the axes because I use the workspace monitoring.
If then you can connect limit switches per axis in series, which does not work with inductive or I have not yet tried.
Why also, is also enough so and needs no other switches.

bbuster2, 2022-04-19:
Thank you for the help, can you explain more what "workspace monitoring" you use?

My idea for multiple switches was to make sure it doesn't go too far in any direction. I was also thinking about putting a limit switch on both Y-axis

Plottmania, 2022-04-19:
In GRBL I have the option for SoftLimits (workspace monitoring).
I use LightBurn, drive a reference, have my zero point at "absolute coordinate" and from there a defined area.
If a workpiece is outside this range, I get a message.
So I don't need a limit switch at the ends of the axes.
One limit switch per axis is enough for the reference run....the rest, as I said, is done by the software.
I also have this option in DrufelCNC and other control programmes.

Sorry for my bad english : )

bbuster2, 2022-04-19:
Thank you and don't worry, your english is good.
I use Fusion360 so i am not sure how i could limit my workspace.

I will buy the limit switches (1 for each axis) and try if i can home and then limit my workspace with softlimits. Maybe the GRBL has bed dimensions built in from the home point?

Plottmania, 2022-04-19:
I haven't tried connecting limit switches in series yet, but it is possible.
Since I only use inductive ones on my DLC controllers: 5 V, GND to signal (range of inductive limit switches here 4 - 30 volts).
But you can connect normal limit switches in series with GND and signal...
If you use a DLC32 either FluidNC or GRBL and there the question which transmitter?
You can specify your working space in the GRBL without any problems.
I know Fusion but don't work with it...I use LightBurn.
But all only for lasering but I think a size can also be defined in Fusion or : )
You only create your file with it and it has to fit into the workspace, no matter which channel.
Anyway, if I have time these days I'll do a test setup for you to see if it works.

Plottmania, 2022-04-19:
Ein kleines Update von meiner SainSmart ProVerXL 4030...demontierte Endschalter und deren Verkabelung.
Kein Plan ob es so funktioniert mit einem DLC32 aber an der Fräsmaschine ohne Probleme mit dem Controller 0/8/15 und GRBL 1.1H

![Uploading IMG_20220419_175826916.jpg…]()

bbuster2, 2022-04-19:
Thank you for showing!
I will see if i can implement it on my own device

Closed 2022-06-02.

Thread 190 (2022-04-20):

Laser ttl output max power

ahmetbozaci, 2022-04-20:
- TTL output support max 25w/50w. Is this laser input power or output power? Because many powerful diode lasers have 30/40/50w input power. If it is so what can we do, should we use the relay module?

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

Plottmania, 2022-04-20:
Then try connecting 24 volts to a laser that has a driver and only likes 12 volts :)
Only very few modules like some Ortur run with 24 volts and 2 amps...because the driver can do this.
If I only connect 12 volts, the fan, for example, will no longer run properly.
But I think if you put 24 volts on a 12 volt board (driver) you won't have any fun with your laser!

Why, because it's too much voltage and the built-in fans don't like too much of it.
Apart from that, there is an output for lasers on the controller and if I do, I buy a laser that can switch 12 / 24 volts, such as the lasers from OptLasers.
In my opinion, however, they do not belong on the spindle and even if they did....wouldn't the laser run permanently there?
What do I do with $32=0 or 1?

manuelchaves, 2022-04-20:
hi, never use a laser, motor or any other high power (W) directly on the board or any other. The ideal is to use a relay (solid or conventional state). It's like 3D printers, you never connect the hots (hotend or hot bed) directly to the board. Go through a power module

See yhis
https://github.com/makerbase-mks/MKS-DLC32/issues/178

ahmetbozaci, 2022-04-20:
@manuelchaves Thank you for your answer. Can ı use mosfet as a relay module?
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

abinoer, 2022-04-28:
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
@ahmetbozaci Hello, what kind of control does your laser head use

ahmetbozaci, 2022-04-28:
@abinoer
For example, this is for neje laser modules. But some laser module has not this board.
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

abinoer, 2022-04-28:
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
The TTL signal is connected to the corresponding pin of the DLC32, and the power supply is external. Do not obtain it from the DLC.

ahmetbozaci, 2022-04-28:
@abinoer Ok what if the laser has not this board. The laser has only 3 pins and it can connect to the dlc32 laser pin very well.
Also, another user said to use a relay, ı was thinking of using MOSFET.

abinoer, 2022-04-29:
Are the three pins TTL, GND and 12V respectively? That is also according to the connection I said above.

Plottmania, 2022-04-29:
Each DLC has a connection for lasers that should NOT be connected via the spindle!
3 pins for 12 V - GND - signal
All laser modules have their own driver and now you just have to check which supplier!
At Ortur there are modules that need 24 volts and max. 2 amps.
But again, a laser does not belong to the connection of the spindle!
The Neje board is an option for Neje laser modules, but you don't really need it!
What it needs and has every driver as an input: 12 volts - GND - signal...you just have to pay attention to the pin assignments.
Fits on every DLC....on every!

VukIgor, 2022-05-10:
I have Mks DLC 32 v2.1 and had issue with laser power ,laser blinking on G moves and my laser module was connected to mks motherboard . Solusion for that issue ,solution for 4wired laser module that is .
laser ( + ) wire conected to external power supply (  + ) terminal , laser signal ( ttl ) wire on S pin on 3pin laser connector on mainboard , laserer ( GND) wire goes to power supply ( - ) terminal  , laser temp wire terminate ,you dont need that .
To get full power of laser module take one wire ,connect one end to ( - ) terminal on psu and other to ( ttl ) pin on mother board where laser connector is ...
Enjoy full power without blinking or low power issues

Skipcruz, 2024-06-06:
@abinoer  foto .... 👀

Closed 2022-05-16.

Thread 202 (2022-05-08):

Bug in schematics

daxliniere, 2022-05-08:
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

Closed 2022-05-08.

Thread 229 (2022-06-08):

Stepper Motors Stall If The Speed Is Over 1500

BigJuicee, 2022-06-08:
I have 2 NEMA 34 stepper motors and they stall if the speed is over 1500 mm/sec. I have the pulse and resolution to where they move the correct distance that I tell it to but I can’t get it to move as fast as a laser should. My stepper drivers are DQ860MA and they are set to 1600 pulse/rev and my X and Y axes travel resolution is 320. I don’t know what I have to adjust so the motors don’t stall and that they move the correct distance.

abinoer, 2022-06-09:
Will stop? What do you mean? Can't move faster than 1500? Could you possibly provide video to see what's going on

solawc, 2022-06-11:
Please ensure that:

1. Your power supply is stable

2. Do you have a 4988 driver in your hand? Have you tested the 4988?

BigJuicee, 2022-06-15:
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

https://user-images.githubusercontent.com/105027332/173854320-0706b7b6-7209-49c1-b766-69e57687cb6c.MOV

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

BigJuicee, 2022-06-15:
The 4988 driver is being used for the z-axis and the NEMA 34’s are being used with the drivers in the photos above.

BigJuicee, 2022-06-16:
When I change the pulse/rev it doesn’t move the correct distance in mm that I tell it to.

abinoer, 2022-06-16:
You can adjust the value of $100, $101, and $102 to get it right

BigJuicee, 2022-06-16:
Wouldn’t that be going up if the motor is set to 1600 for the pulse/rev?

abinoer, 2022-06-16:
If the distance is not correct, just adjust $100, $101, and $102

BigJuicee, 2022-06-16:
What should I have the current to the motors set to?

abinoer, 2022-06-16:
This needs to be set according to the load and motor parameters, so I can't give you any suggestions

Closed 2022-06-16.

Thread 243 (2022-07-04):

problema minimo pwm

distebia, 2022-07-04:
salve, ho un problema con una mks dlc32 v2.1 e firmware 2.08 e 2.10 per laser normale board 2.0. il problema è che non riesco ad accendere il laser sotto il 10%. con macchina arduino montato nella stessa andavo a variare il parametro mandrino_pwm_min_value contenuto in config.he impostavo il valore di 25 per aggiungere mV all'uscita pwm, per avere la minima accensione.
i miei parametri su arduino uno sono $30=255, $31=0. Con arduino configura in questo modo accendo il laser al 1%. Con mks dlc32 v.2.1 non ho modo di fare la stessa cosa in quanto non ho il config.h. Ho trovato il parametro $28 che, momentaneamente, ho lasciato a 1000, $35 che dovrebbe essere l'equivalente di mandrino_pwm_min_value ma variandolo non ottengo differenze. Ho anche impostato $31=100 ma accendo sempre il laser intorno al 10% e, anche variando $30, $31, $35, $28 non ottengo variazioni di emissione pwm.
tutto questo sia con lasergrbl che con lightburn (LB configurato come da $30). è come se la scheda memorizza i valori dati ma non li esegue, o li esegue entro un certo limite.

distebia, 2022-07-05:
ho un co2 50w e ho montato arduino uno grbl 1.1h. nel pin pwm per raggiungere 0.2v e accendere il tubo al minimo dovevo commentare il valore del config.h   //spindle_pwm_min_value=25 per accendere. uso $30=255, $31=0. smonto arduino e monto la mks dlc32 v2.1.
imposto $30=1000, $31=100 (non posso commentare il config.h) e se invio g1m3s100f1000 il laser si accende. $28 lasciato a 1000 di default. invio g1m3s90f1000 il laser non si accende. in tutto questo se imposto il $35 con valori 10,20,30 non ottengo variazioni. tutto questo comporta che, in modalità m4, ho dei cerchi e quadrati incompleti in quanto si spegne quando rallenta.

distebia, 2022-07-05:
> Perché non puoi sparare laser al di sotto del 10%? Inviare l'istruzione "M3 S50 G1 F1000" non funziona? 50/1000 = 5%

non funziona, non accende. ho bisogno di alzare mV per l'uscita minima e raggiungere 0.2V al 1%

abinoer, 2022-07-06:
You said so much, but I still don't understand what you need, you set these parameters for what

distebia, 2022-07-06:
vorrei essere in grado di accendere il laser al 1%, attualmente lo accendo al 10%. inoltre se effettuo un taglio al 10% ho delle interruzioni in prossimità degli angoli o dove la macchina rallenta. se non correggo questo la macchina per me è inutilizzabile

distebia, 2022-07-07:
esiste un firmware per laser normale che mi da la possibilità di variare i parametri inerenti l'uscita pwm? grazie

distebia, 2022-07-09:
un conto è un firmware chiuso dove non posso cambiare indirizzi hardware o velocità processore ecc... un conto è impedisce dei settaggi basilari. da come ho capito tutti dobbiamo avere lo stesso alimentatore che si accende allo stesso modo, accetta la stessa frequenza di pwm. Se ho comprato il vostro prodotto completo di monitor lcd perchè devo mettere un altro firmware perdendo altri benefici?

distebia, 2022-07-13:
> Hai detto tanto, ma ancora non capisco di cosa hai bisogno, hai impostato questi parametri per cosa

esiste una soluzione al mio problema?

Closed 2023-09-09.

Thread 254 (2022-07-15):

Z axis drops down after soft homing

dedeca, 2022-07-15:
My MKS DLC32 2.1 board has been a struggle with coding, after the new update V2.1.0_H24_20220511_01_N_CNC.bin the option of manually moving Z axis over wifi has gone, so a few drill bits are gone.
Reversed back the firmware to the V2.0.8_H24_20220108_N_CNC.bin being an CNC application I believe Makerbase haven't made ever any firmware to the board 2.1 of the DLC32 model.
my machine is a simple 3018 having the Z going UP/DOWN, X LEFT/RIGHT and Y BACK/FORWARD.
The lazer cable came with 2 different end's, after using with external power supply noticed that when had to change for CNC, now fixed the cable PWM working fine, however the fan of it is always on, I need to check later when moving to lazer again, for now focusing in cnc.
**Now the issue here is the machine after pressing soft home and at the end select new job to print, it DROPS FURTHER DOWN digging in what is not meant to, howerver this does not happen if machine after homing been turn OFF and ON again to start a new job!!**
My screen is a TS24 and to run my motor I'm using a SS relay and power supply, here is my config file:    short one on the end

/***************************************************************************/
DLC_TEST=0        //Model： 0：Usage mode， 1：Test mode
/********************************************************************************/

/***************************************************************************/
*--------------Machine parameter format："$x=y"
*--------------Function configuration format："[ESPXXX]yyy"
*--!!!WARNING!!!--*
*------1.Do not change the value of x in the machine parameter format at will,
         otherwise a configuration error will occur and it will not start
*------2.Can't add configurable items at will
/*******************************************************************************/
// (Step pulse time：Sets time length per step. Minimum 3usec.)
$0=10
// (Step idle delay:Sets a short hold delay when stopping
// to let dynamics settle before disabling steppers.
// Value 255 keeps motors enabled with no delay.)
$1=25
//---Basic parameter setting-----//
//(Step pulse invert)
$2=0
//(Step direction invert)
$3=5
//(Invert step enable pin)
$4=0
//(Invert limit pins)
$5=1
//(Invert probe pin)
$6=0
//(Status report options)
$10=1
//(Junction deviation)
$11=0.010
//(Arc tolerance)
$12=0.002
//(Report in inches)
$13=0
//(Soft limits enable)
$20=0
//(Hard limits enable)
$21=0

//---Zero setting----//
/(Homing cycle enable)
$22=0
//(Homing direction invert)
$23=0
//(Homing locate feed rate)
$24=250.000
//(Homing search seek rate)
$25=500.000
//(Homing switch debounce delay)
$26=250.000
//(Homing switch pull-off distance)
$27=1.000
//(Maximum spindle speed)
$30=10000.000
//(Minimum spindle speed)
$31=0.000

//---Protection function setting----//
//(Laser-mode enable)
$32=0
//(Flame  1:Turn on,0:close)
$37=0
//(Beep 1:Turn on,0:close)
$38=1
//(Gyro 1:Turn on,0:close)
$39=0
//(Set Language, 0: ch, 1:en 2:de)
$40=1
//(Roller 1:Turn on,0:close)
$41=0

//(X-axis travel resolution)
$100=800.000
//(Y-axis travel resolution)
$101=800.000
//(Z-axis travel resolution)
$102=800.000

//---Speed setting----//
//(X-axis maximum rate)
$110=100.000
//(Y-axis maximum rate)
$111=100.000
//(Z-axis maximum rate)
$112=1000.000
//(X-axis acceleration)
$120=50.000
//(Y-axis acceleration)
$121=50.000
//(Z-axis acceleration)
$122=20.000
//(X-axis maximum travel)
$130=300.000
//(Y-axis maximum travel)
$131=180.000
//(Z-axis maximum travel)
$132=80.000

//--WIFI configuration---//
[ESP110]STA
[ESP131]8080
//wifi name
[ESP100]	000000000
//wifi password，00000000：[ESP101]

/*---modify2021-11---*/

$0=10
$1=25
$2=0
$3=5
$4=0
$5=1
$6=0
$10=1
$11=0.010
$12=0.002
$13=0
$20=0
$21=0
$23=0
$24=250.000
$25=500.000
$26=250.000
$27=1.000
$30=10000.000
$31=0.000
$32=0
$37=0
$38=1
$39=0
$40=1
$41=0
$100=800.000
$101=800.000
$102=800.000
$110=100.000
$111=100.000
$112=1000.000
$120=50.000
$121=50.000
$122=20.000
$130=300.000
$131=180.000
$132=80.000

dedeca, 2022-07-16:
turns out the file was made wrong

Closed 2022-07-16.

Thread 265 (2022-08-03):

Isnt somebody smart enough?

manitoulin-maker, 2022-08-03:
HERES A GREAT IDEA EVERYBODY!

Why dont we all try to decipher the board since MKS wont. there is no reason for them to not release the pins for this board. we are all loyal to them even tho they wont release it. im not sure if i would call it "false promises" , because im not sure they ever said they would, regardless, they shouldnt have to, this is all "OPEN-SOURCE" so i think they should really rethink their place in this market.

ANYWAYS !!!, ....  I see the half-a$$ pinout they have so far. i count a good amount of IO Pins that are listed, maybe we can figure the rest out with some reasoning, somewhat like what jailbreaking apple, im not saying lets exploit ANYTHING, what i am saying, is, since it is open source, cant we try to work our way through the firewalls persay.

Heres my idea:

  from the given IO pins, we can work out what pins are left, and they try to work out the logical places for those IO pins from either like chipped boards, or just deductive reasoning, now i dont want anybody to fry thier boards, so we should limit pin checking to the low voltage ones from cross checking the pinout of the ESP chip.        Just an idea, as i am getting EXTREMELY TIRED OF MKS'S BULLSH#T.

I am okay at compiling, adding some new features but really i am still at a user level with configuring marlin, in no way do i understand how c++ works or anything other than you need defines and .h files thats IT. so, i/we need all of your help, please. we all can do this!! look at what other groups do when they come together, we are all makers! please for the sake of the human race, lets figure this out ugh!!!  i wanna make sh#t with my 9 yr old son for the love of frig.

manitoulin-maker, 2022-08-03:
Found out some more pins last few hours, i will post my findings tomorrow. i have 4 of these boards SO ILL TRY TO BE AS MUCH OF A HELP AS I CAN,

Lasermax3000, 2022-08-07:
I would also like to help, but actually i don´t have the time and the opportunity to measure which Pins from the ESP32 go out to which Plugs. But if anyone can figure it out, i can help to develop a simpler Opensource Firmware which works better than this current BULLSH#T.

manitoulin-maker, 2022-08-07:
That's all we need. Anybody that can even help a tiny tiny bit is all we
need to do this
 Maybe if we get close. They will just release it.  Through looking at some
other firmware for the dlc32. There's about 20 pins defined already.
Fluidnc is where I. Getting a lot of I do as they have compiled for that.
We will get it guys.

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

keithstrachan, 2022-08-09:
the main issue is the LCD screen. The functional pins are already working in other firmware, like GRBL-Hal and FluidNC, but no one has the LCD working... this is the main problem.

kweilim98, 2022-08-10:
> the main issue is the LCD screen. The functional pins are already working in other firmware, like GRBL-Hal and FluidNC, but no one has the LCD working... this is the main problem.

yaaa, agree with u

keithstrachan, 2022-08-10:
i think that what is needed to start, is to
1. find an example to use LCD with ESP32 chip, and see how that related to io pin usage.
2. append the grblhal code into the lcd screen code to create the new platform.

i believe that is why it is hard, because people are looking at the grbl side first, and i think that it needs to look at the lcd side first.
i'm not a programmer, but i think this way logically works

keithstrachan, 2022-08-10:
touch appears to be based on TSC2046 / ADS7846 touch screen controller. not sure if the xpt2046 library will drive this, but i believe they're the same family.
probably using the TFT_eSPI driver to run the screen

Medina-ui, 2022-08-10:
Hi. I want to help on this because I have several boards and tft's are arriving soon ( but I don't have a lot of free time ) . About the screen, I am not sure because TFT's are still on the way, but maybe this is  not a big problem.... Check this board (MKS TinyBee) , same ESP32-WROOM-32U and TFT possibilities (MKS35) with two 10pin conections cables, and that is clear for me that all logos,bitmaps and "letters" are on Marlin/GRBL side, just like Arduino with LCD12864. And libraries are available for this on the link:  https://github.com/makerbase-mks/MKS-TinyBee/tree/main/firmware

keithstrachan, 2022-08-11:
> Hi. I want to help on this because I have several boards and tft's are arriving soon ( but I don't have a lot of free time ) . About the screen, I am not sure because TFT's are still on the way, but maybe this is not a big problem.... Check this board (MKS TinyBee) , same ESP32-WROOM-32U and TFT possibilities (MKS35) with two 10pin conections cables, and that is clear for me that all logos,bitmaps and "letters" are on Marlin/GRBL side, just like Arduino with LCD12864. And libraries are available for this on the link: https://github.com/makerbase-mks/MKS-TinyBee/tree/main/firmware

Hi Medina,
There are many examples of using the standard mks tft35 screens because they run their own processor, stm32f4 etc.
This is easy to get going.

The TFT screen supplied with the MKS-DLC32 is a MKS TS35-R which does not have it's own firmware or processor, but uses a driver and is controlled by the DLC32 ESP chip.  Similar design to the TS35-E3, TS35 and PI-TS35 - these all use SPI to control screen and touch.

the MKS TFT/TS repo is here: https://github.com/makerbase-mks/MKS-TFT-Hardware
you can look at the schematics to see what i mean

Medina-ui, 2022-08-11:
Hi

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

HI Keithstrachan, I understand exactly what you mean. I think you did not understand me, but no worries, as soon as my TFT35 R arrives I will test "my theory" and share.

giordy72, 2022-08-21:
Look at the schematics for pins and connections.
Switch to fluidnc or gribl Hal, and forget the unusefull tft. Use an old smartphone as hmi  and your up to go in half an hour.

keithstrachan, 2022-08-21:
thank you for your unusefull comment giordy72, so small minded, can't see the bigger picture

Medina-ui, 2022-08-30:
Hi guys, I had a look on MKS documents and compare V1.1_0001 SCH and PIN Documents are there are a lot of mess on pins description/assignment . Also I had a look on V2.1_003 Documents and this one have only one pin that is diferent on both documents. In the file you can see in red the diferent information on both files for the same board, and on orange a strange assignment. Does MKS want to give us fake information?
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

keithstrachan, 2022-08-30:
> Hi guys, I had a look on MKS documents and compare V1.1_0001 SCH and PIN Documents are there are a lot of mess on pins description/assignment . Also I had a look on V2.1_003 Documents and this one have only one pin that is diferent on both documents. In the file you can see in red the diferent information on both files for the same board, and on orange a strange assignment. Does MKS want to give us fake information? 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

@medina-ui its not fake information when there is a typo in the document. I have been over these as well, and there are mistakes, but i believe they are honest accidental mistakes, not deliberate. Deliberate mistake (fake information) is if they put information that is contrary to a truth, making a lie.
You must also remember that for many people, english is not first language, and when you are typing on a keyboard in a hurry, sometimes you forget to type a letter, number, symbol.. just like in your post, you spell "different" incorrectly :)

So far, the only thing wrong is that MKS indicated that they would release the source code, and they have not.
during any PCB development, just like code development, the designer/writer will make small changes to optimise the artefact. this is why they have v1, v2 etc.  When you compare v1.1 of a design against v2.1 - you should expect variations

But also keep this in mind. Any code, grbl, grbl-hal, fluidNC, marlin etc - have config files to allow the specification of the pins to allow tweaking to align (fix up mistakes) in the physical board.
if the software was completely hard coded, then we would be in real big trouble.

kweilim98, 2022-08-31:
https://github.com/solawc/ESP32_LaserBox_E/blob/main/GRBL/src/Machines/i2s_out_corexy_mks_dlc32.h

I not sure here the Pin out able to help u or not because I am not familiar to coding, but here is about the MKS dlc32 xyz pin out, u can check it out at here

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

makerbase-mks, 2022-11-15:
Code open source late but finally here: https://github.com/makerbase-mks/MKS-DLC32-FIRMWARE

Closed 2022-11-15.

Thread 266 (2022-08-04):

When I connect my Limit switch machine shuts down. When switch is pressed comes on

growlybearproductions, 2022-08-04:
I don't know if this is a hardware or software issue. The switch has an LED. When switch is engaged the LED comes on

When switch is NOT engaged the system only has the main power light Everything else shuts off. If I press the switch all lights come back on.

keithstrachan, 2022-08-09:
what it seems like is that your pins are not matching up and you have a short.
I would disconnect them to prevent any damage to your board, and then you need to check your wiring for your switches.

many of the limit switches have pins swapped around because they're wired for RAMPS boards. You need to make sure that GND from the switch, comes to GND on the DLC board, voltage to voltage, signal to signal.

the wiring manual located [here](https://github.com/makerbase-mks/MKS-DLC32/blob/main/doc/DLC32%20wiring%20manual.pdf)
is quite easy to understand and follow.

good luck.

Closed 2022-08-29.

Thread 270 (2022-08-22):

frimware Laser V2.10_H35_2022_0621_N_ZX_001.bin

Wieslaw68, 2022-08-22:
V2.10_H35_2022_0621_N_ZX_001.bin Laser. Invalid x + / x- direction in control.

hans-de, 2022-08-23:
Same problem here. The x direction between display and PC control is reversed. No Idea which of them is right. I hope it will be fixed soon. However, it would be better to release the source, the community can do this faster.

hans-de, 2022-08-25:
After a week of fruitless attempts with several firmware versions to bring the board into a usable configuration, I give up. The board goes back. Too bad, because the hardware itself is very usable.
I think this was my first and also my last MKS Board.
With every new Firmware version they fixed some bugs and added new one.

Wieslaw68, 2022-08-25:
I don't know why they don't want to share resources, the community would have fixed it long ago.

tbsmnea, 2022-08-26:
The hardware as such is ok. The touch display also makes a good impression, but unfortunately there is no option to rotate the display by 180 °. Unfortunately, the software is full of bugs and MKS is probably not interested in resolving it. The decision for the board a lot for me to improve the good price, the super fast CPU and the WLAN support. Unfortunately, the programmers don't even get distinguished right and left. The X directors are exchanged via the display control. The over 70 bugs, which have also been reported on GitHub for months, speak a clear language here. I think the community could fix the bugs in a short time, but unfortunately the souce code is not accessible. For me, this is probably the first and last MKS board and if I don't get the board to run at short notice, it goes back. Unfortunately, I wasn't aware of that before. It's a shame about time.

iherbak, 2022-09-08:
I uploaded the firmware amd set up wifi, but the web ui is unable to load up. Any solutions? I had to revert the previous one to get it work

iherbak, 2022-09-10:
> Same problem here. The x direction between display and PC control is reversed. No Idea which of them is right. I hope it will be fixed soon. However, it would be better to release the source, the community can do this faster.

You have to edit the settings that's all, here is the default:

$0=10 (Step pulse time)
$1=25 (Step idle delay)
$2=0 (Step pulse invert)
$3=2 (Step direction invert)
$4=0 (Invert step enable pin)
$5=0 (Invert limit pins)
$6=0 (Invert probe pin)
$10=1 (Status report options)
$11=0.010 (Junction deviation)
$12=0.002 (Arc tolerance)
$13=0 (Report in inches)
$20=0 (Soft limits enable)
$21=0 (Hard limits enable)
$22=0 (Homing cycle enable)
$23=0 (Homing direction invert)
$24=25.000 (Homing locate feed rate)
$25=500.000 (Homing search seek rate)
$26=250 (Homing switch debounce delay)
$27=1.000 (Homing switch pull-off distance)
$30=1000 (Maximum spindle speed)
$31=0 (Minimum spindle speed)
$32=1 (Laser-mode enable)
$100=80.000 (X-axis travel resolution)
$101=80.000 (Y-axis travel resolution)
$102=250.000 (Z-axis travel resolution)
$110=2000.000 (X-axis maximum rate)
$111=2000.000 (Y-axis maximum rate)
$112=2000.000 (Z-axis maximum rate)
$120=6000.000 (X-axis acceleration)
$121=6000.000 (Y-axis acceleration)
$122=10.000 (Z-axis acceleration)
$130=200.000 (X-axis maximum travel)
$131=200.000 (Y-axis maximum travel)
$132=200.000 (Z-axis maximum travel)

iherbak, 2022-09-10:
> For me it was the first time, not working either. I downloaded the web Ui, just an empty website, SD card, and the web UI, newly loaded, and see it has worked. Apparently there is also a bug that does not work with the SD card for the first time. After that I didn't have to remove the SD card anymore

without sd it fires up. But as soon as i put sd in it kills itself. I reverted back to the previous version.

capi92, 2022-09-18:
> V2.10_H35_2022_0621_N_ZX_001.bin Laser. Invalid x + / x- direction in control.

Same here

abinoer, 2023-01-07:
It has been resolved, please update the firmware

Closed 2023-01-07.

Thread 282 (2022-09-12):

Laser module cooling fan always on

drkline, 2022-09-12:
Hello,
I have installed DLC32 boards on two laser machines and both of them have their laser module cooling fans running at 100% always.  The laser modules are Sculpfun S9 and S10.  I have had them both installed on a Ortur LaserMaster 2 and its control board and never had this issue.  What do I need to do to have the cooling fan run only when the laser is turned on?  Leaving it like this will eventually wear out the small DC fan on the laser module and I don't want this to happen.  Please let me know what I need to do.

Thank you,
Dave Kline

Plottmania, 2022-09-14:
This is normal and also good!
Unfortunately, mostly too thin cable collapses the performance.
Either a thicker cable and optionally a really good fan on it and neither the driver nor the LED get warm.
Really good it is with TEC and Peltier and we have about 22 degrees which helps a premature death or aging of the LED.
S10 with Peltier under full load 18 hours run without problems and no performance drop.
Sorry for my bad English

drkline, 2022-09-14:
Thank you Stephan,

So are you suggesting to have a cooling fan for the stepper drivers to keep them cool?  And what gauge wire would you suggest using for the laser module power?

Sincerely,
Dave

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

Plottmania, 2022-09-15:
Sculpfun S10 - Peltier-Cooling and correct cables

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

After a runtime of 18 hours under full load with 100% power measured: 10.2 watts optical output power.
The S10 from Sculpfun is a nice toy!

onehans1, 2022-10-18:
Maybe is good for you but for some not 🙉
Question stands. How to stop it from running at full whack non stop?
Original Atomstack board do not run when not needed.
Mks DLC32 v2.1 as soon i power it it goes crazy for no reason

hans-de, 2022-10-19:
Based in my knowing this ist not possible. But at least a cool laser is better than a hot. To make it save you musst also measure the temperature. 
Gesendet von Yahoo Mail auf Android

  Am Di., Okt. 18, 2022 at 21:40 schrieb ***@***.***>:

Maybe is good for you but for some not 🙉
Question stands. How to stop it from running at full whack non stop?
Original Atomstack board do not run when not needed.
Mks DLC32 v2.1 as soon i power it it goes crazy for no reason

—
Reply to this email directly, view it on GitHub, or unsubscribe.
You are receiving this because you are subscribed to this thread.Message ID: ***@***.***>

onehans1, 2022-10-19:
$S+ or $S pops up option where ~"TurnOnFanWhen LaserRunning=off" changing it to "on" doesn't affect state of fan

abinoer, 2023-01-07:
@drkline
The motherboard output of 12/24V is a constant output, uncontrollable, this board can not do laser open to open the cooling fan

onehans1, 2023-01-07:
I'm talking about laser output pins S V G
Laser fan runs at full speed.
Atomstack frame A5 used fan speed according to laser power output strength

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

Closed 2023-01-07.

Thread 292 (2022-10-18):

Reversing X-Y displacements on the TS-35-r display

FMD14, 2022-10-18:
I just installed an MKS DLC32 v 2.1 card with a TS-35-R screen with the latest version CoreXY frimware V2.10_H35_2022_0704_C_ZX_001.bin
On the screen the movements are reversed while on laserGrbl or lightburn and the web application move in the right direction
How to solve this problem?

manuelchaves, 2022-10-18:
Hello, change the position of the wires in the connectors of the stepper motors

hans-de, 2022-10-18:
Thats a Bug. The Display control xchange the direction. You can live with it, Install an older version with Others Bugs or wait for s fixed version. I decided the 4st Option. Return to sender and by a better board. The Hardware is pretty good, but the Software made me crazy.

Gesendet von Yahoo Mail auf Android

  Am Di., Okt. 18, 2022 at 12:23 schrieb ***@***.***>:

I just installed an MKS DLC32 v 2.1 card with a TS-35-R screen with the latest version CoreXY frimware V2.10_H35_2022_0704_C_ZX_001.bin
On the screen the movements are reversed while on laserGrbl or lightburn and the web application move in the right direction
How to solve this problem?

—
Reply to this email directly, view it on GitHub, or unsubscribe.
You are receiving this because you are subscribed to this thread.Message ID: ***@***.***>

FMD14, 2022-10-19:
I just installed version 2.08 the axes work
But I can't configure my limit switches
How to fix this problem
I just requested a refund for the card and screen
Which 32-bit card should I buy for CoreXy
because I feel like MKS does nothing to fix bugs
They are there to sell and that's all

FMD14, 2022-10-20:
I just asked for the refilling of the card and the screen near the seller is not winning
Which 32-bit card should you turn to have correct results for corexy laser

abinoer, 2023-03-03:
The display moving x backwards has been fixed

abinoer, 2023-03-03:
The display moving x backwards has been fixed

stephendaley, 2025-08-30:
how was it fixed

Closed 2023-03-03.

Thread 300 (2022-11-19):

Problem MKS DLC32 with K50 laser co2 no fire

alstare72, 2022-11-19:
Hi there …

 I have K50 upgraded version of K40
 New power supply and adjustable bed

 I bought mks Dlc32 v2.1 board

 The K50 uses a black box power supply of MYJG60W
 Terminal block different from Ķ40
 FG AC AC ok

 And secondary terminal block H L P G IN 5V

 And I have a 2nd card above the general power supply which feeds the NanoM2 card with Green 24v, Black GND, Red 5V, and Yellow L wires.
 I removed the nano card...
 I took Black and Green to power the MKS ok
 Motor connected ok
 S from MKS to IN
 in lightburn and lasergbl:
 Movement with arrow up down left right ok until ALARM:2

 Lack of co2 laser signal …

 The internet assembly images indicate spindle - to G and Ttl to L

 Ttl on L burns directly at 19ma

 If I add Spindle - to G nothing more
 …

 Laser power problem and lightburn do not want to run my test rectangle ALARM:2
  I tested another assembly that I saw here on ķ40 but still the same the laser burns directly at 20ma continuously as soon as I press the Laser switch
 sorry i use the translator
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

abinoer, 2023-01-07:
I don't quite understand what you mean. Is it convenient for you to join QQ group 650031716 for communication

3Dangel, 2023-01-08:
Don't use the TTL to fire the laser. instead use the Spindle's one.
Search for k40 -Mks-DLC32 and you will see.... and only one line. but you would need to power your DLc32 with the same powr supply so the Ground is in common to the laser and to the DLC32. good luck. (also search LB forum using the sear criterial.

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

alstare72, 2023-01-09:
Merci pour votre aide ..

J'ai changé la carte par avataar120  ..

Sujet clos..
Merci encore

Closed 2023-01-09.

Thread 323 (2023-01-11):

Board Random Resets

ArcAIN6, 2023-01-11:
So.. I've tried everything to eliminate the issue, but i'm at a loss, perhaps someone could give some advice.

No matter what i do, the board will just randomly reset itself.

Things i've tried:

1) Replaced all cables and wires with shielded versions. Tried both WIFI & USB: Still Resets
2) Disabled all Homing / Limit features in the settings (disabled auto home, disable hard and soft limits). Tried both WIFI & USB: Still Resets
3) Disconnected the Spindle, used a GCode with just movement (no spindle). Tried both WIFI & USB: Still Resets
4) Replaced the PSU, Tried both WIFI & USB: Still Resets
5) Replaced the Fuse, Tried both WIFI & USB: Still Resets
6) Replaced motor drivers, Tried both WIFI & USB: Still Resets
7) built firmware to replace the stock firmware that was on it (firmware grabbed from here) Tried both WIFI & USB: Still Resets

I honestly have no clue what's going on with this board. It's almost like the ESP32 is reaching a computation limit, and watchdog is resetting it, but i have no idea how to check to see if that's the case.

Anyone have suggestions on what to try next?

ArcAIN6, 2023-01-11:
UGS platform has a setting for limiting the length of code sent to the controller, dropping it from 70 to 40 and machine makes it all the way through a small test engraving without issue.

Closed 2023-01-11.

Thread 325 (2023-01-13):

Probe Target Flame Error

concuus, 2023-01-13:
Hello, first of all I use translation. Sorry if there is any confusion. I'm either missing something or doing something wrong as there isn't enough documentation in my native language, any help would be appreciated.
I am trying to make a CoreXY diode laser. For this, I use SculpfunS9 laser with MKS DLC32 V2.1, TS35 and TMC2209 set.
Since the bench I assembled is not on the scale, I installed the necessary swich and probe to measure with the probe.
I measure with the "G38.3 Z70 F200" command, but when the probe is triggered, I get the following error;

G38.3 Z77 F200
[MSG: Found]
[PRB:450,000,450,000,000,70,086:1]
arrow
[MSG:Flame error! Please restart the machine]

As far as I researched and understood; The $37 command turns the fire sensor on and off. However, the code $37 appears to be disabled in the assembly numbered V2.30_H35_2022_1223_C_ZX_001 that I installed

37 dollars
error:3
The grbl '$' system command is not recognized or supported.
$37=0
error:3
The grbl '$' system command is not recognized or supported.

I would be glad if you could help me on the matter.

Additionally, I use Air Assist. Related Pin connections are correct but the system is working in reverse. It opens with M9 and closes with M7. Is there a Gcode that will reverse this cycle?

I don't know if it's because of the compilation, but I wanted to point that out. The "dlc_cfg.txt" I saved to the memory card is not read at startup. but when I load previous builds it reads the relevant txt at startup.

Thanks in advance.

concuus, 2023-01-19:
I guess this didn't happen to anyone.

MJ666, 2023-02-17:
I have the same error when trying this firmware with an Atomstack x20. This is using an LaserBox ESP32 V1.0 board which is likely a clone of the MKS DLC32.  If i use the prebuild firmware for an MKS V1.0 board everything is working except the laser does not fire. If I use an firmware fro the MKS V2.0 board i get this error "[MSG:Flame err!Please restart the machine]" and the board looks up after a few seconds and does not respond anymore. I found no way how to disable or control the fuction of the probe pin. The only difference between MKS V1.0 and V2.0 boards are the probe and spindle (laser pwm) pins. I try to use this firmware since the Atomstack firmware does not support M9, M8 and M9 commands to control the I2C SCL pin.

abinoer, 2023-02-27:
@concuus
1. Warning about FLAME: The laser firmware has no probe function, because the io used for probe detection is used for flame detection in the laser firmware

2. About air assistance: M7————scl pin high level, M9——————scl pin low level, so it is necessary to choose NMOS module as the switching module

Closed 2023-02-27.

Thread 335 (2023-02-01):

Mid dlc32 v2.1 laser is always on

danielfrausto, 2023-02-01:
Help. My flashed the laser corexy firmware and laser is always on. Constant power. Setting $32=0 won't turn off

rd636, 2023-02-08:
I have the same issue.  The 12-24V-PWM type (2PIN) is constantly producing 12 volts (or 24 volts when using that power input voltage) immediately at startup and not turning off.   Nothing else seems to be impacted.  Drives motors fine.  Homing is still working.  LCD working.

danielfrausto, 2023-02-08:
> I have the same issue.  The 12-24V-PWM type (2PIN) is constantly producing 12 volts (or 24 volts when using that power input voltage) immediately at startup and not turning off.   Nothing else seems to be impacted.  Drives motors fine.  Homing is still working.  LCD working.

Hello there, I was able to fix this issue by sending the commands
M4 S0
Then
M5
And finally
M4 S0 again.
Hope this works for you too.

rd636, 2023-02-08:
Thank you for the suggestion but it did not resolve the issue.
M4 S0
ok
M5
ok
M4 S0
ok

villamany, 2023-02-09:
what pins are you using?. PWM is TTL level not 12/24v

rd636, 2023-02-10:
I think the board is bad.  I replaced the board, upgraded it, and am not experiencing the issue.   I think we can close this out.

maadmackz, 2023-02-11:
im having this to just suddenly, it was fine and then i hit buffer mAX it froze and now laser on all th8e timje, s to in,  ttl to L , gonna try that with spindle - to ground?  and external psu grounded to lpsu both grounded to case. both grounded to AC ground.

sharknetwork24, 2023-06-07:
I have the same problem too.
Everything works perfectly except that the laser is always on and to turn it off I have to disconnect the general power supply.
I would like to know if the problem has been solved, or if it is a defect of the Board DLC32 v2 that does not work.
Can it be solved or should the BOARD be replaced?
Thanks for the replies.

Closed 2023-02-27.

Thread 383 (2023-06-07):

DLC32 v2 Laser is always on

sharknetwork24, 2023-06-07:
Everything works perfectly except that the laser is always on and to turn it off I have to disconnect the general power supply.
I would like to know if the problem has been solved, or if it is a defect of the Board DLC32 v2 that does not work.
Can it be solved or should the BOARD be replaced?
Thanks for the replies.

sharknetwork24, 2023-06-07:
I connected everything correctly.
I attach image of the laser module where the DLC32 v2 board is connected to the laser module

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

sharknetwork24, 2023-06-08:
Is it possible to have a wiring diagram to understand where the problem lies?
And the mosfet to replace Q1 (WSF40N10)?
On J18 I always have a voltage of 12.35V

Ho trovato questo ma non so se è corretto.
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

3Dangel, 2023-06-10:
don't use the TTL
USE THE Spindle.
if you found the schematic of v2.x then chech with the schematic of V1.x and you will see the differences between the two.
V 1.x will work. V2.x won't.

sharknetwork24, 2023-06-10:
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

Is the spindle output ok to control the laser?
So you're telling me that the 3-pin TTL output doesn't work in version 2.1 boards?

sharknetwork24, 2023-06-10:
If anyone knows how to make the links please use the picture and re-post with the correct links.
Other people may benefit.
Thank you

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

sharknetwork24, 2023-06-13:
May be of help to others who have the same Laser.

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

Closed 2023-06-22.

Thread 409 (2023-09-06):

Another M4 error with DLC32 V2.1.003

guyjami, 2023-09-06:
Hi everybody.

I have replaced an eleksmana SE with a DLC32 V2.1.003. Everything works fine but the laser. I tried a lot of things from other subjects in the forum and posts on internet but nothing worked for me.

When connected , the DLC returns
[ORIGIN:China]
[PRODUCER:MKS_DLC32]
[DATE:20220905]
[VER:1.1h.2023052701:]
[OPT:VPHSW,15,256]
Target buffer size found
[MSG:Machine Name:MKS DLC32]
[MSG:Mode=AP:SSDI=MKS_DLC:IP=192.168.4.1:MAC=24-DC-C3-0A-11-AD]

On the DLC32 H35 screen :
Board:MKS DLC32 CNC V2.1
V2.3(8M.H35.20230527)
CPU:Freq:240MHz/ T:50.0C/ ID:44049

When i try to start a stream with lightburn or lasergrbl, i get the following message :
[MSG:M4 requires laser mode or a reversable spindle]
error:20
Unsupported or invalid g-code command found in block.

The laser mode is well activated $32=1
Don't known where the problem is ?
Any idea ?
thank's

mv-83, 2023-10-26:
i have same problem,almost certainly the problem is the latest firmware

guyjami, 2023-10-27:
It was in fact a firmware issue.
The V2.3(8M.H35.20230527) provided with the board had issue with m4 command event the laser mode ($32=1) is enabled.
I have flashed the board with an older one (V2.30_H35_2022_1223_N_ZX_001.bin) downloaded here on github :[https://github.com/makerbase-mks/MKS-DLC32/tree/main/firmware/TS35/Laser/Normal/Board_V2.0 10](https://github.com/makerbase-mks/MKS-DLC32/tree/main/firmware/TS35/Laser/Normal/Board_V2.0)
Now it works perfectly with lightburn and M4 command even via USB and TS35 Screen connected !

guyjami, 2023-10-27:
Finally, i just changed the value $23 from 5 to 3 to have the same origin position than lightburn.
So my old eleksmaker A3 is more silent, capable of working standalone or via wifi, able to drive a rotary module and can do homing via limit switches.

mv-83, 2023-10-27:
> It was in fact a firmware issue. The V2.3(8M.H35.20230527) provided with the board had issue with m4 command event the laser mode ($32=1) is enabled. I have flashed the board with an older one (V2.30_H35_2022_1223_N_ZX_001.bin) downloaded here on github :[https://github.com/makerbase-mks/MKS-DLC32/tree/main/firmware/TS35/Laser/Normal/Board_V2.0 10](https://github.com/makerbase-mks/MKS-DLC32/tree/main/firmware/TS35/Laser/Normal/Board_V2.0) Now it works perfectly with lightburn and M4 command even via USB and TS35 Screen connected !

bad for me, I had to compile the source code to swap the pins of the Y axis with those of the Z axis (on the board there are 2 connectors for the Y motors, but I have 2 motors in the Z axis) and I don't know where look for the bug

guyjami, 2023-10-29:
you can wire your two Z motors in parallel. That's what i've done on my ender 3 v2 when i have added a second Z motor. It exist cable adapters to do the job.

dhuff0271, 2025-05-17:
I think it's here
https://github.com/makerbase-mks/MKS-DLC32/blob/main/MKS-DLC32-main/firmware/TS35/Laser/Normal/Board_V2.0/V2.30_H35_2022_1223_N_ZX_001.bin

Closed 2023-10-27.

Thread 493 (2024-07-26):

Need Help: Connecting MKS DLC32 v2.1 to CO2 Laser PSU

Benglin, 2024-07-26:
Hi MKS team and community experts, I will try to make this post as clear as I possibly can so you can help me out. These might be beginner questions so please bear with me... 🙂

## My MKS DLC32 v2.1

Few points about my **MKS DLC32 v2.1**:

-   It is powered by 12V DC
-   I have never flashed any new firmware so it's the default
-   I am afraid to connect it to CO2 laser PSU due to the observation below about signal voltage

-   ❓ **Question 1**: why is the output for `S` in `S, TTL, V` measured to be `0 ~ 12V`? (I know we can't quite measure PWM signals with a digital multi-meter, but its value should not have gone way beyond `5.00V` if it is meant to be within `0 ~ 5V`).

The [document](https://github.com/makerbase-mks/MKS-DLC32/blob/main/MKS-DLC32-main/doc/DLC32%20wiring%20manual.pdf) says it should be `0 ~ 5V` as shown below:

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

-   ❓ **Question 2**: should I use a step-down mechanism to bring it down from `0 ~ 12V` to `0 ~ 5V`?

-   ❓ **Question 3**: would refreshing with the latest firmware fix the issue (I can try that when I return to it next week)?

## My CO2 Laser PSU

Not wanting to destroy my [laser PSU](https://www.aliexpress.com/i/32818973603.html), I made my [Arduino Uno](https://store-usa.arduino.cc/products/arduino-uno-rev3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) output PWM signals of `0 ~ 5V` through a PWM pin `9`, here's how I connect the wires (I am sure the PWM signal is `0 ~ 5V` using a digital multi-meter, and an associated LED that fades in and out):

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

-   ❓ **Question 4**: Should I even be using that `5V` output on the laser PSU? It seems to be an _"output port"_

-   ❓ **Question 5** Is it because I did not connect `WP` to `G`? If so I'm gonna be so pissed with myself now

The above connection is inspired by the following wiring diagram that has been shared in various places before (I just replaced the potentiometer with PWM that's coming from an Arduino Uno, it will be changed to MKS DLC32 v2.1 when wiring confusion is sort out)

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

Thank you all for spending the time to read this, any help I get would really be appreciated. Thanks again team 😄

**Side note**: I have read [the other thread](https://github.com/makerbase-mks/MKS-DLC32/issues/48) where `Flipcnc` came very close to a solution (with help from great folks like @makerbase-mks, `3Dangel`, `maadmackz`, `matonhodze` and many others). I did not want to add more noise to the thread so I decided to start a new question here (I hope that is okay).

costycnc, 2024-07-27:
https://www.youtube.com/shorts/79jmSSWvY7w

Benglin, 2024-07-27:
Thanks for the tip, @costycnc! That looks neat 👍

I see it uses `SPINDLE (-)` to drive the PSU, which is something I might want to try out too (based on the [documentation](https://github.com/makerbase-mks/MKS-DLC32/blob/main/MKS-DLC32-main/doc/DLC32%20wiring%20manual.pdf) it should produce `0 ~ 12V` signal for me, I'm not sure if my LPSU can handle that, I'll check with Cloudray).

The only thing I can't tell from the video is which port does the `SPINDLE (-)` connect to in the LPSU (as K40 one is quite different from [mine](https://www.aliexpress.com/i/32818973603.html)). But thanks anyway for your help!

costycnc, 2024-07-28:
i have inspired from this video https://youtu.be/xfqtSgPIYKg?si=ajWVxvMtEqqSMOA0&t=382

Benglin, 2024-07-30:
Thanks again for your help, @costycnc! Your video prompted me to measure the spindle's voltage (unfortunately that is also ranging from `0 ~ 12V` when my laser PSU expects an input signal of `0 ~ 5V`), then re-measure the power output of the `S-TTL-V` ports. It turns out that, unlike my original claim in my question above, the `S` pin does output `0 ~ 5V` PWM signals! I think my previous measurements were wrong due to some bad wiring.

In any case, it turns out that I did not connect `P` (water protect) to `GND` on the laser PSU. Since the water protection is not a closed circuit, the laser PSU refuses to fire the tube. After connecting `P` to `GND`, everything works perfectly!

The diagram below illustrates the correct way to connect my laser PSU to the MKS DLC32 board (note that the pins on MKS DLC32 are incorrectly labeled as `S-TTL-V` when they should really be `S-GND-V`):

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

And to answer my own questions in the original post:

-   💡 **Answer 1**: The `S-TTL-V` pins on the MKS DLC32 board are wrongly labeled; they should really be `S-GND-V`. My previous readings on these pins were wrong. The `S` (signal) pin correctly outputs `0 ~ 5V` as documented, and `V` outputs a constant `12V` or `24V` depending on the input voltage to the MKS DLC32 board.

-   💡 **Answer 2**: Since the `S` pin correctly outputs `0 ~ 5V` PWM signals, no step-down is required.

-   💡 **Answer 3**: I didn't get to try the latest firmware, and I don't have a reason to do so right now, so this remains a mystery.

-   💡 **Answer 4**: The `5V` on the laser PSU actually outputs a constant `5V`, and there's no use for it in my scenario.

-   💡 **Answer 5**: This is exactly the reason. I did not connect `P` (water protect) to `GND`, causing the laser PSU to "think" that the water protection system is "broken," therefore refusing to fire the laser tube.

jlbarros76, 2024-08-12:
Hi Benglin, what a wonderful work . I have a 150W PSU and 100W CO2 Laser tube, can I use this connection (the last one) without problem? I´m stuck finding a solution to make functional my diy cnc laser engraver. Can I use with laser grbl o lightburn? Waiting your comments, thank you.

Benglin, 2024-09-02:
Hi @jlbarros76, I'm sorry for not seeing your question earlier! I am not certain of what the issue you are facing with, can you explain a little more and also show us how the connection is made? I might not be able to help you (because I am a beginner also) but others should be able to 🙂

By the way, I am having an issue myself also, the final connection works, but I realized the laser is firing even when I just turned on the laser PSU. I am not sure what is the problem here but I will continue to debug it (because it did work before with my Laser Web).

Closed 2024-07-30.

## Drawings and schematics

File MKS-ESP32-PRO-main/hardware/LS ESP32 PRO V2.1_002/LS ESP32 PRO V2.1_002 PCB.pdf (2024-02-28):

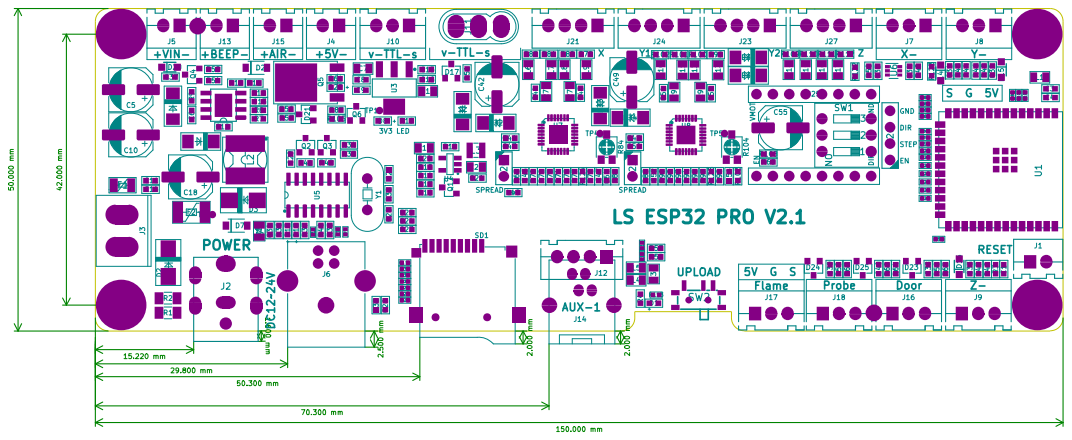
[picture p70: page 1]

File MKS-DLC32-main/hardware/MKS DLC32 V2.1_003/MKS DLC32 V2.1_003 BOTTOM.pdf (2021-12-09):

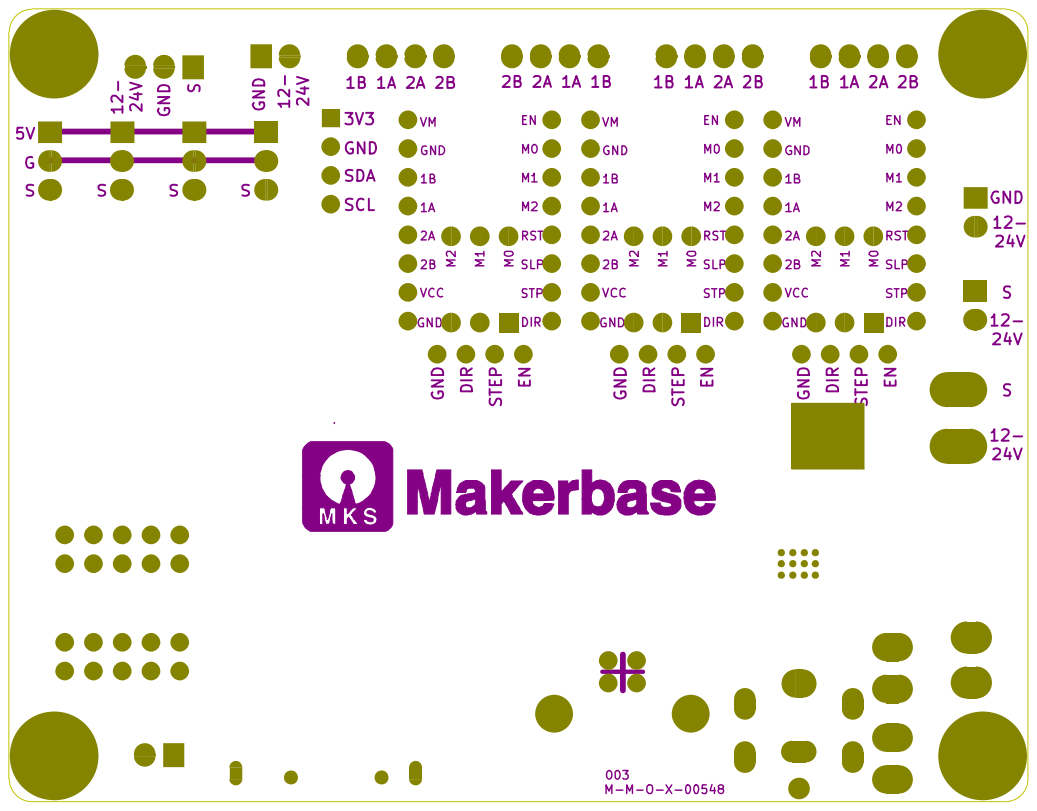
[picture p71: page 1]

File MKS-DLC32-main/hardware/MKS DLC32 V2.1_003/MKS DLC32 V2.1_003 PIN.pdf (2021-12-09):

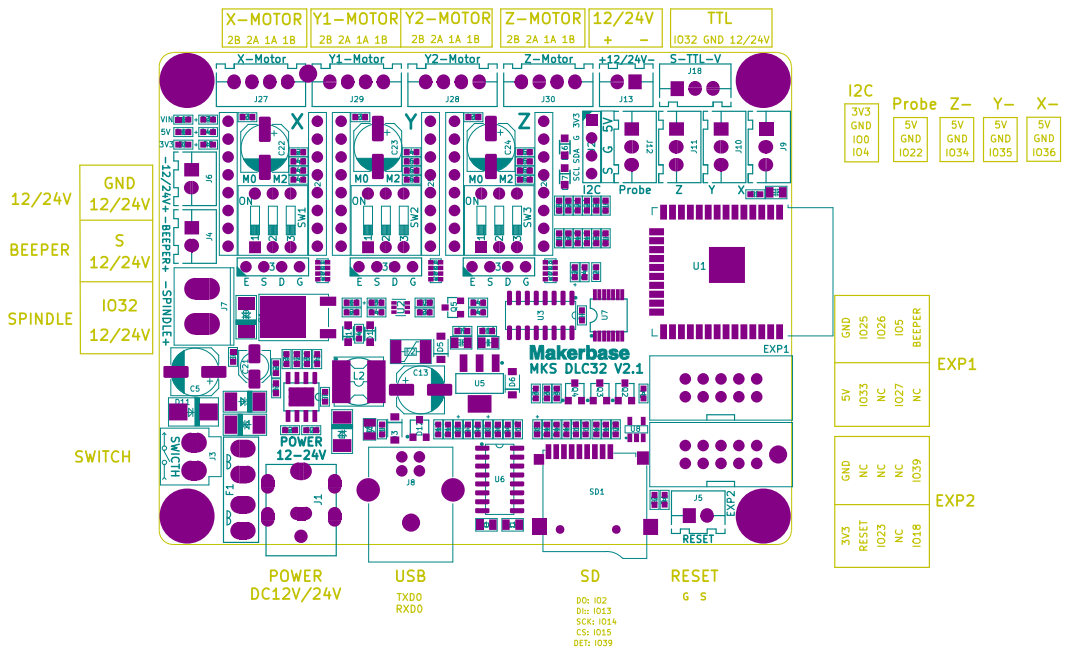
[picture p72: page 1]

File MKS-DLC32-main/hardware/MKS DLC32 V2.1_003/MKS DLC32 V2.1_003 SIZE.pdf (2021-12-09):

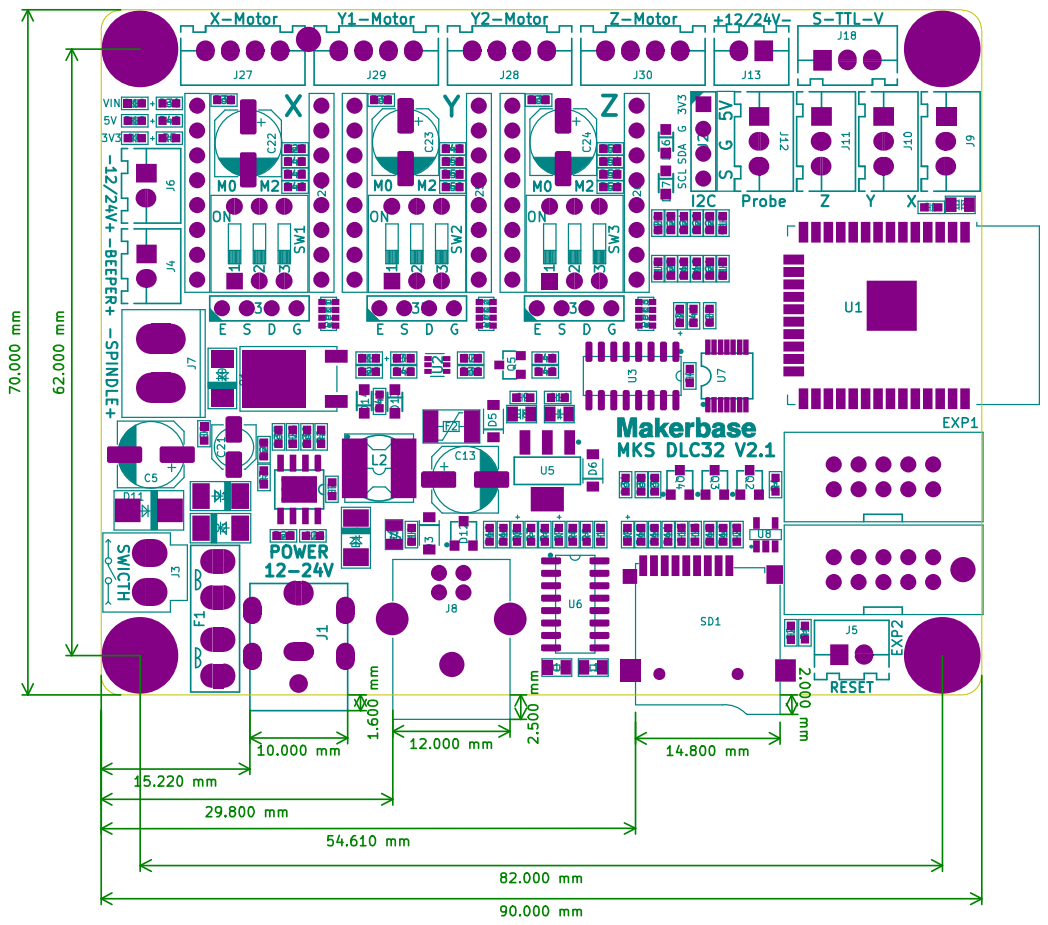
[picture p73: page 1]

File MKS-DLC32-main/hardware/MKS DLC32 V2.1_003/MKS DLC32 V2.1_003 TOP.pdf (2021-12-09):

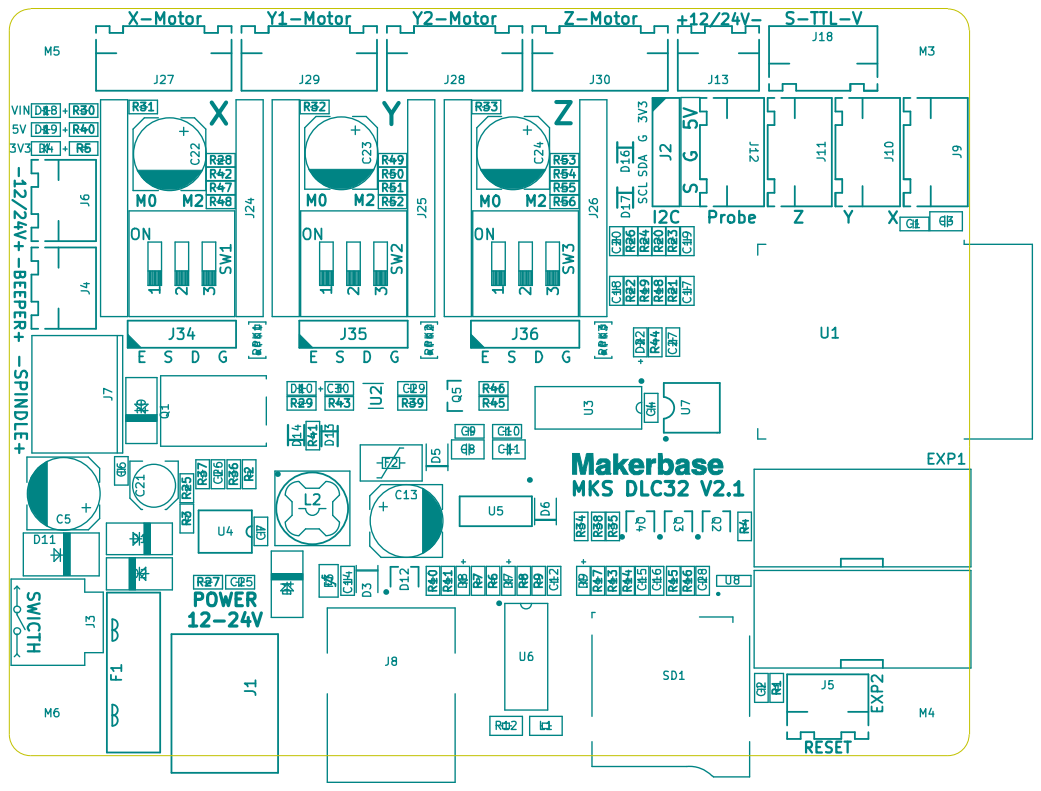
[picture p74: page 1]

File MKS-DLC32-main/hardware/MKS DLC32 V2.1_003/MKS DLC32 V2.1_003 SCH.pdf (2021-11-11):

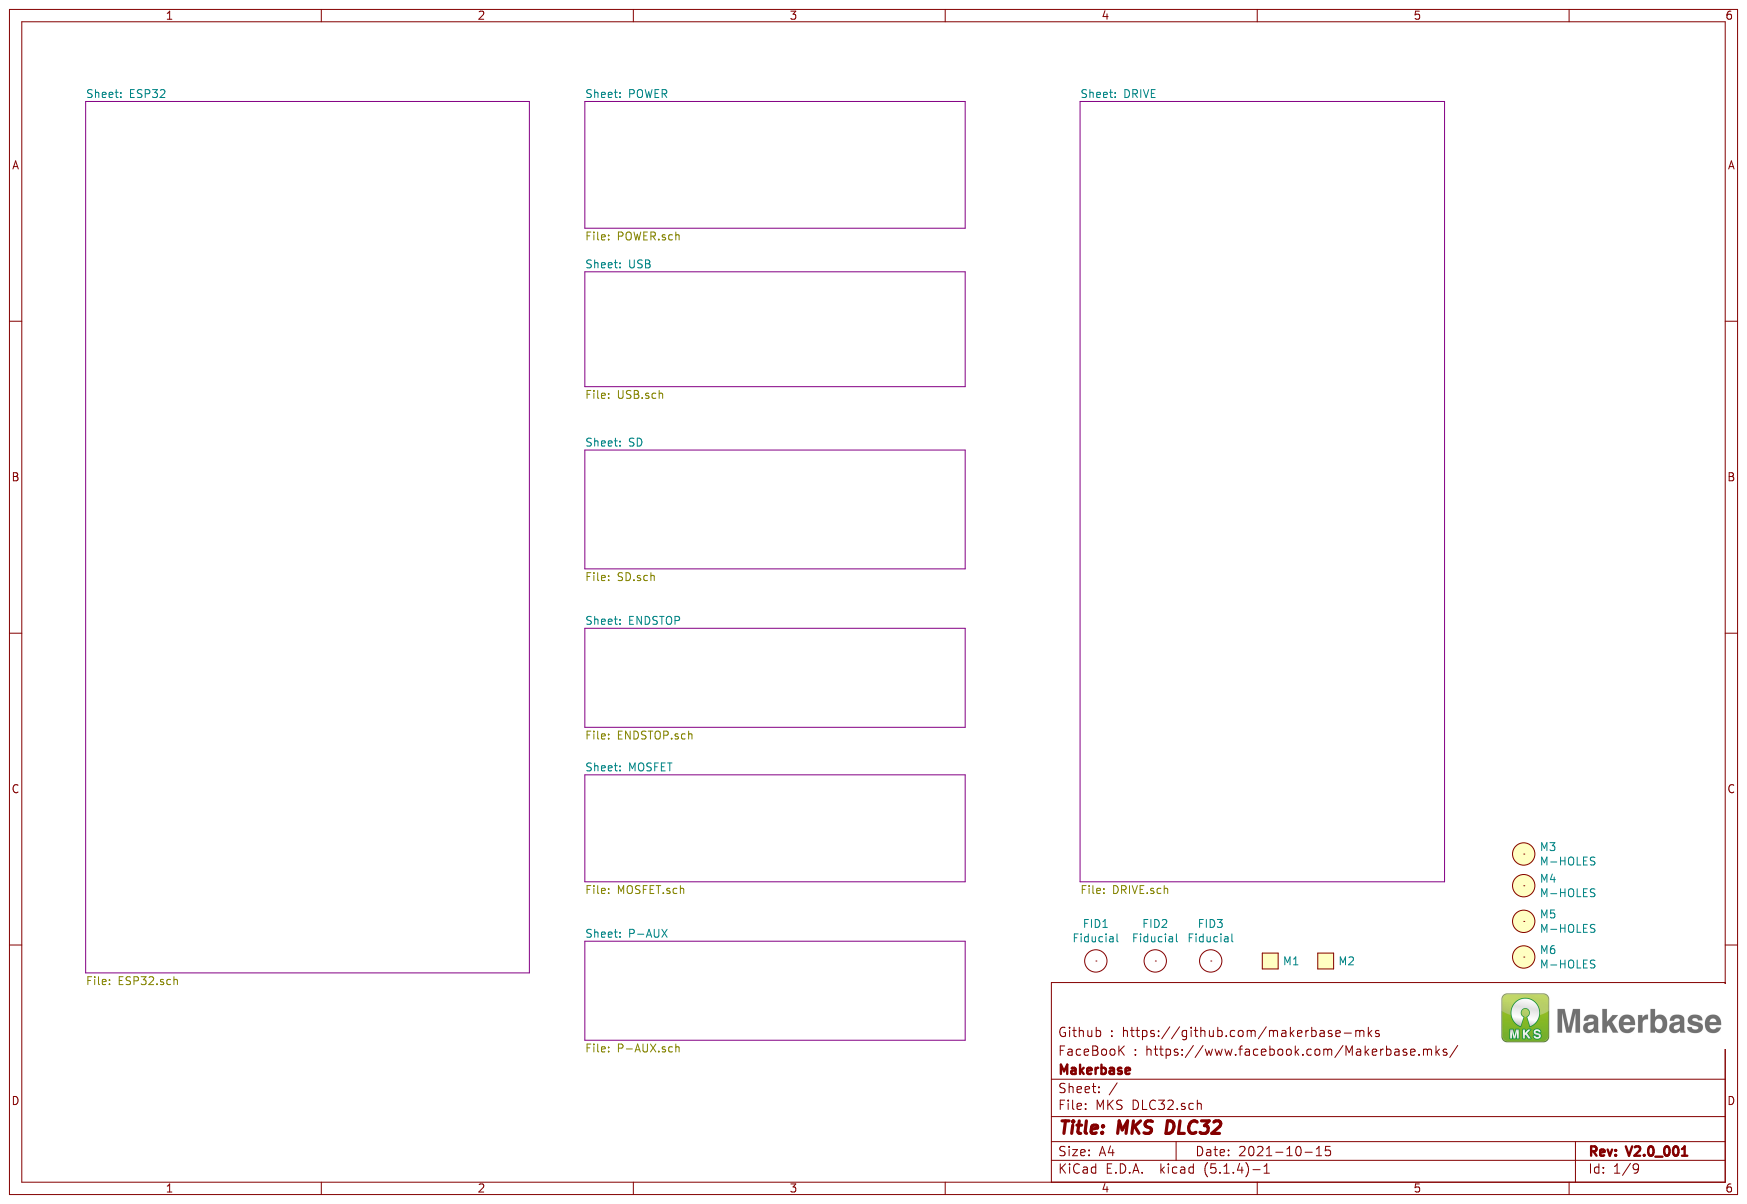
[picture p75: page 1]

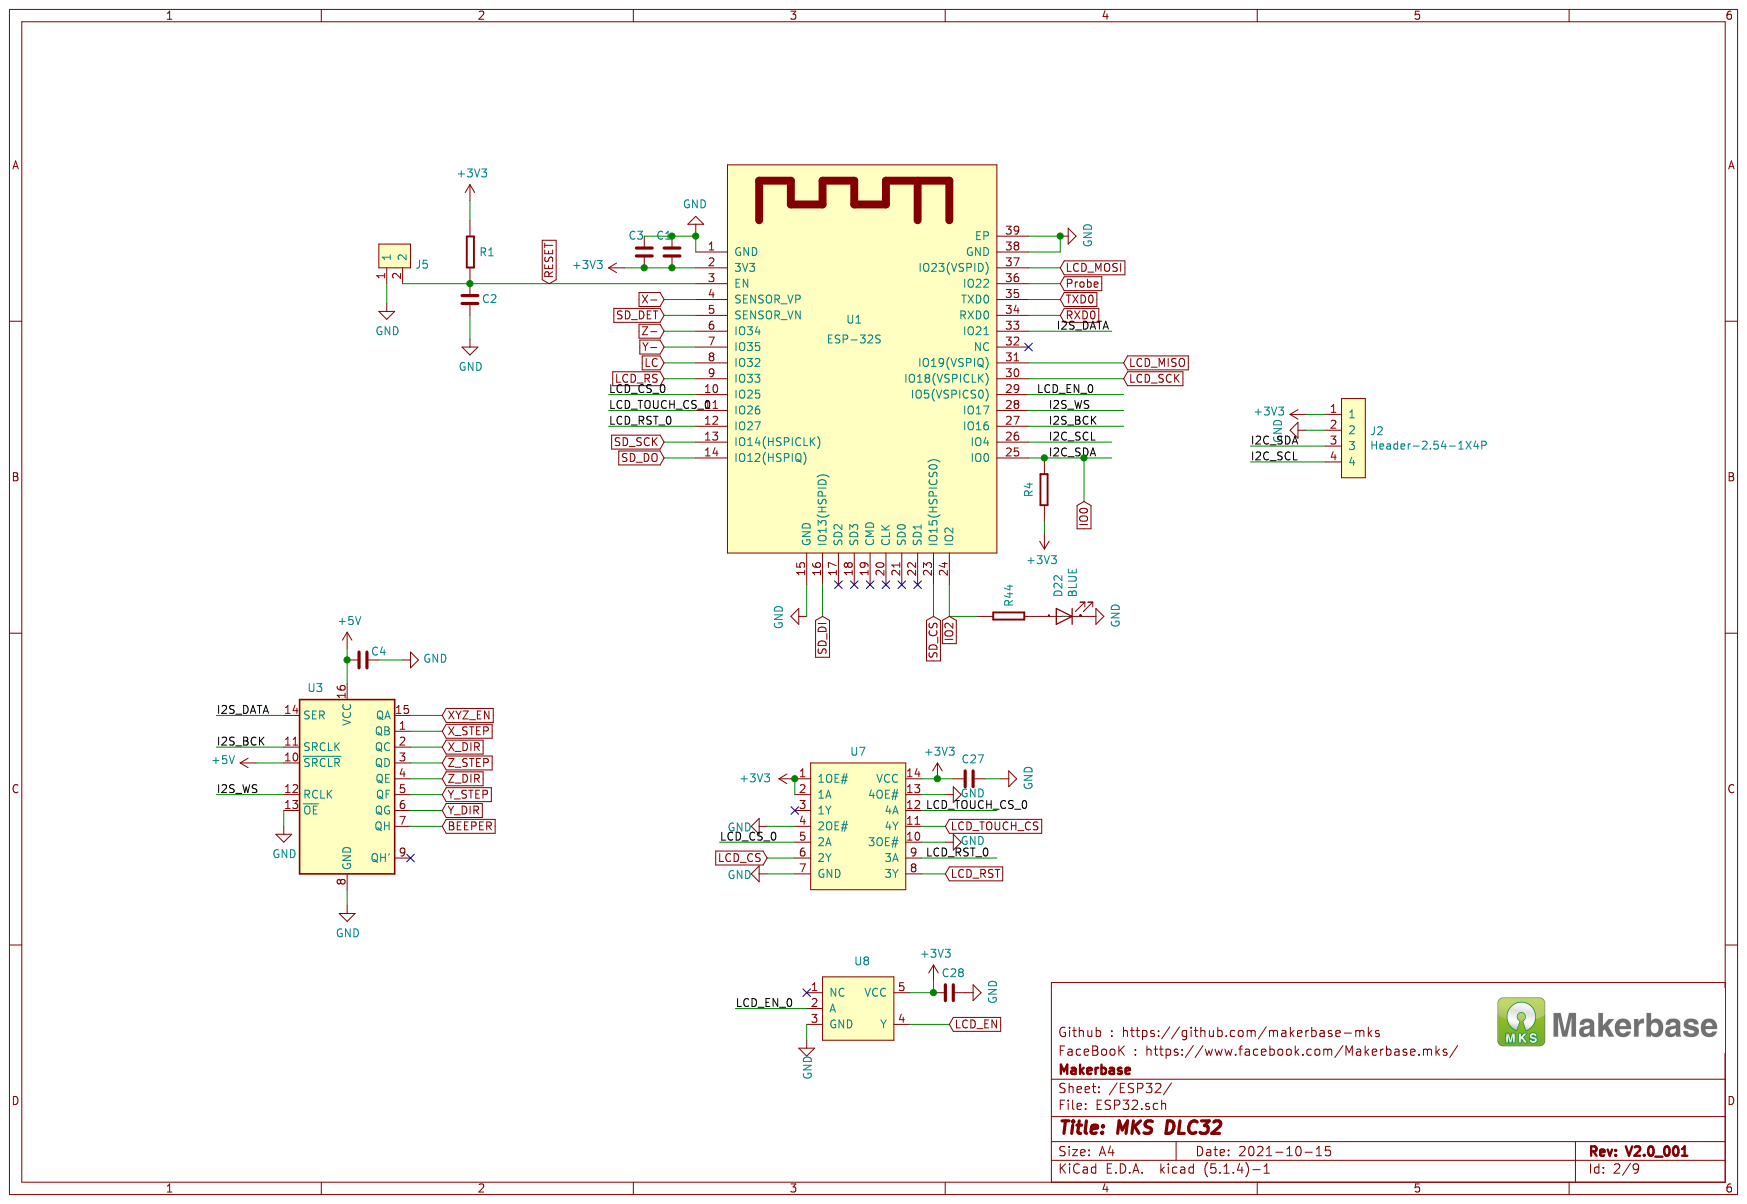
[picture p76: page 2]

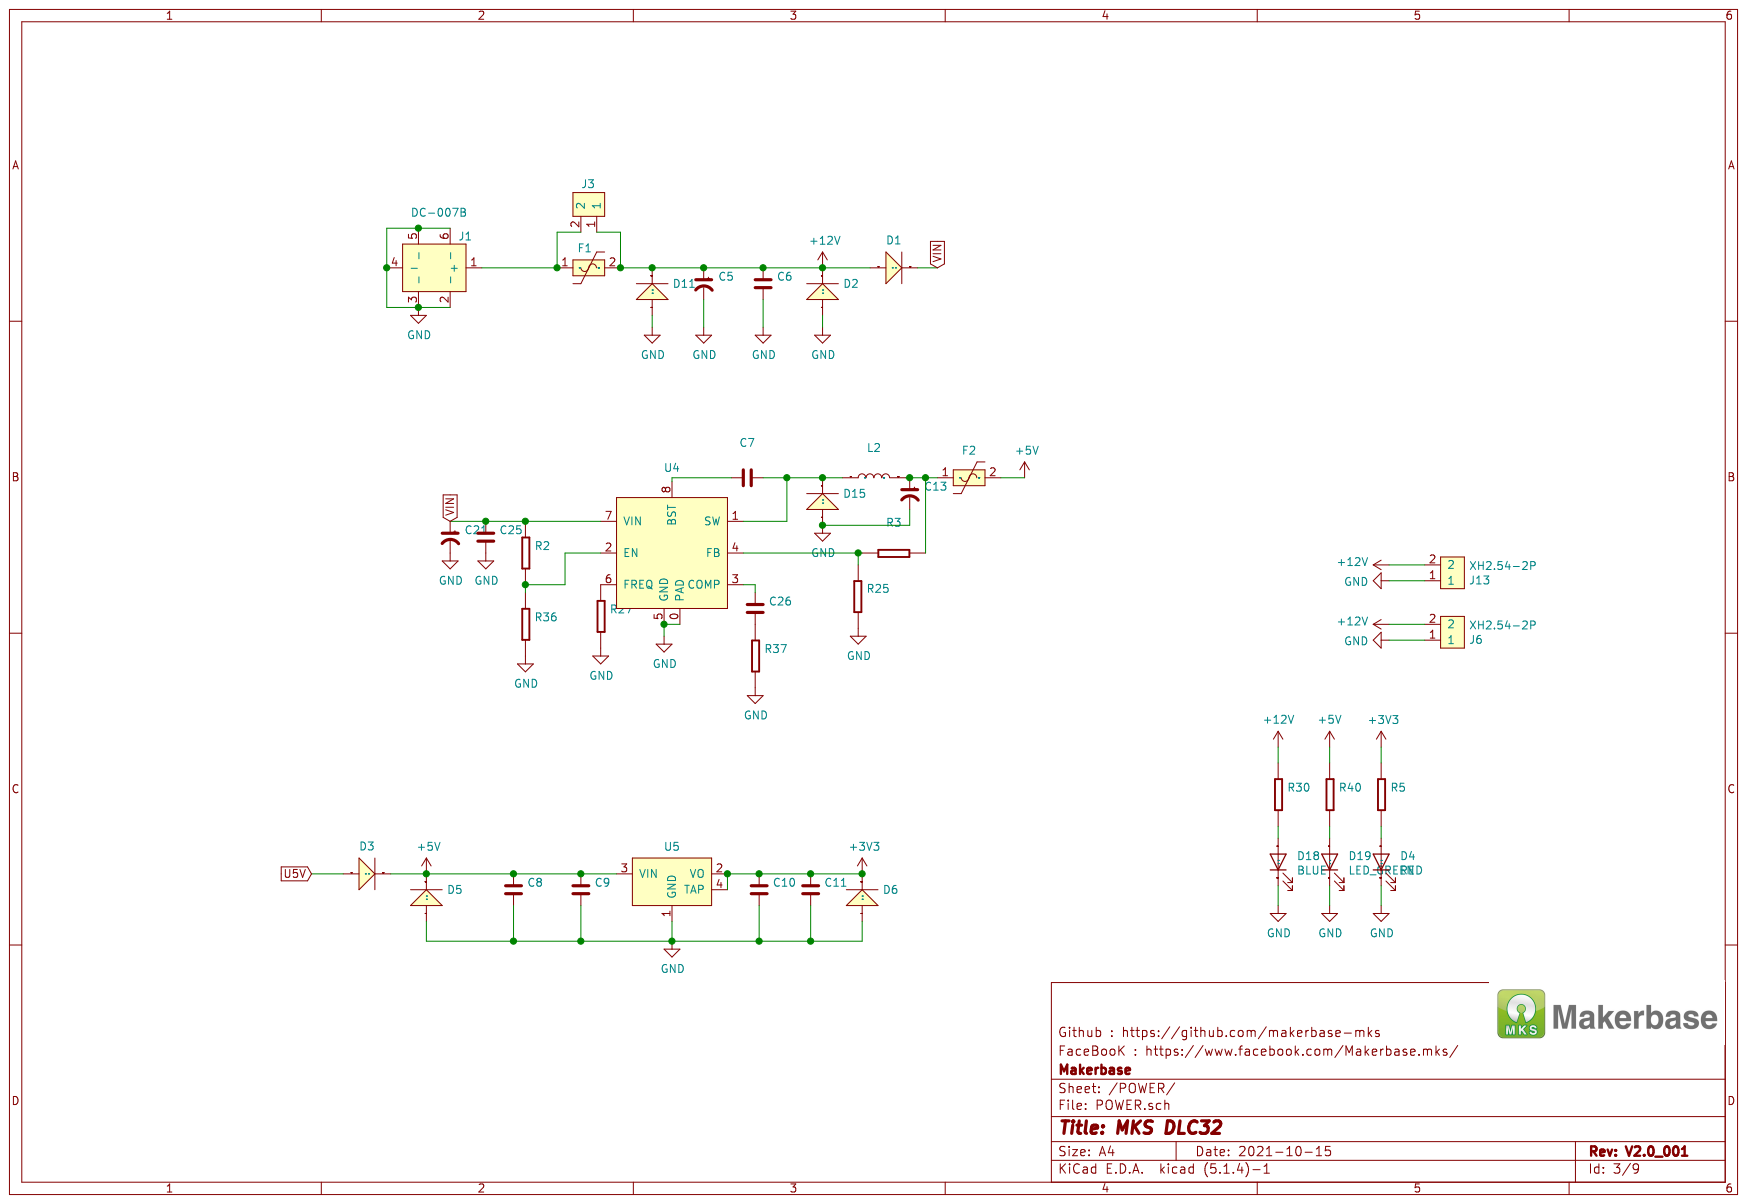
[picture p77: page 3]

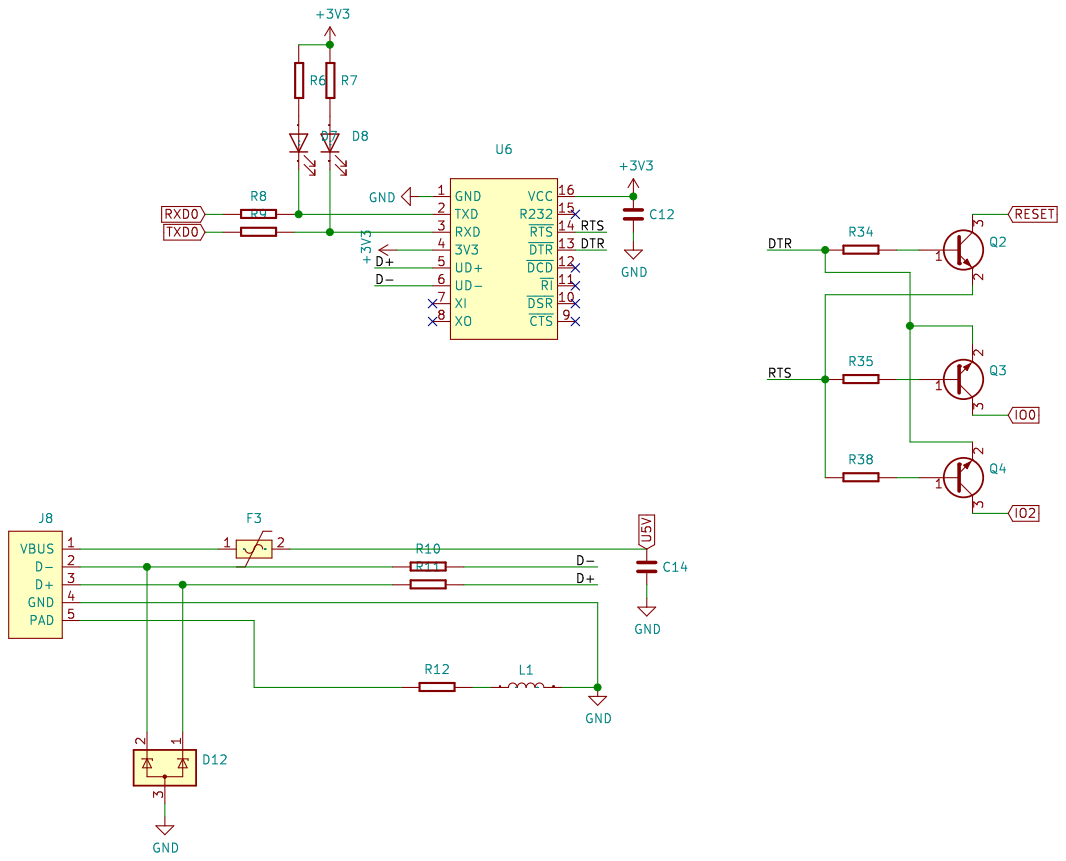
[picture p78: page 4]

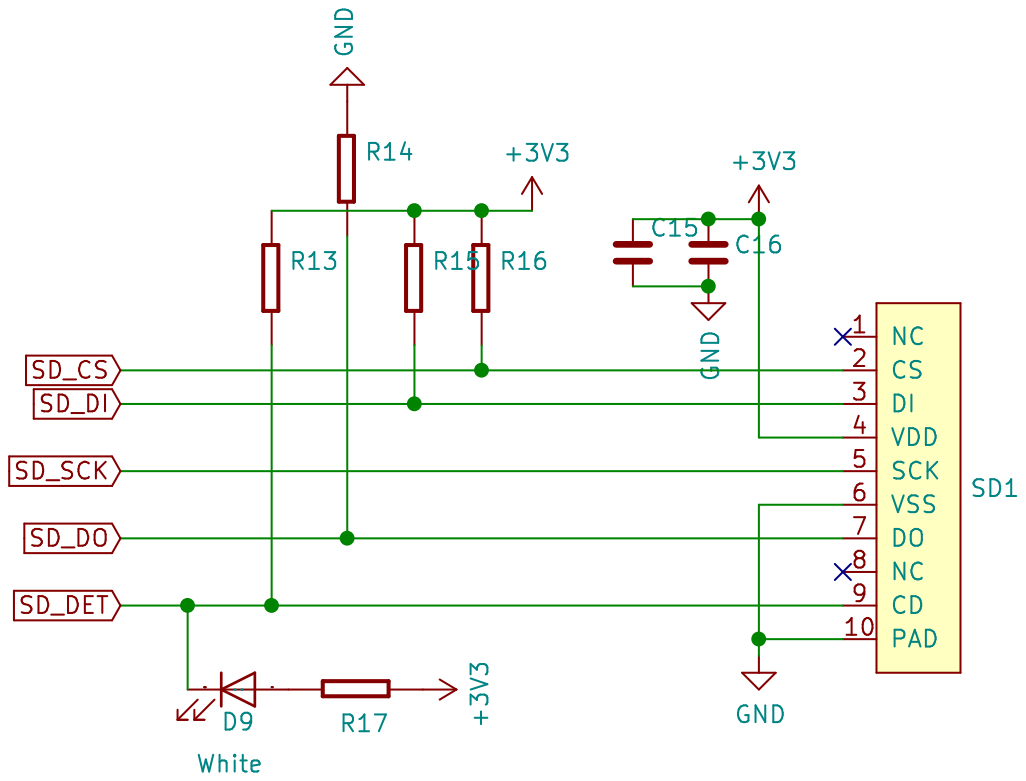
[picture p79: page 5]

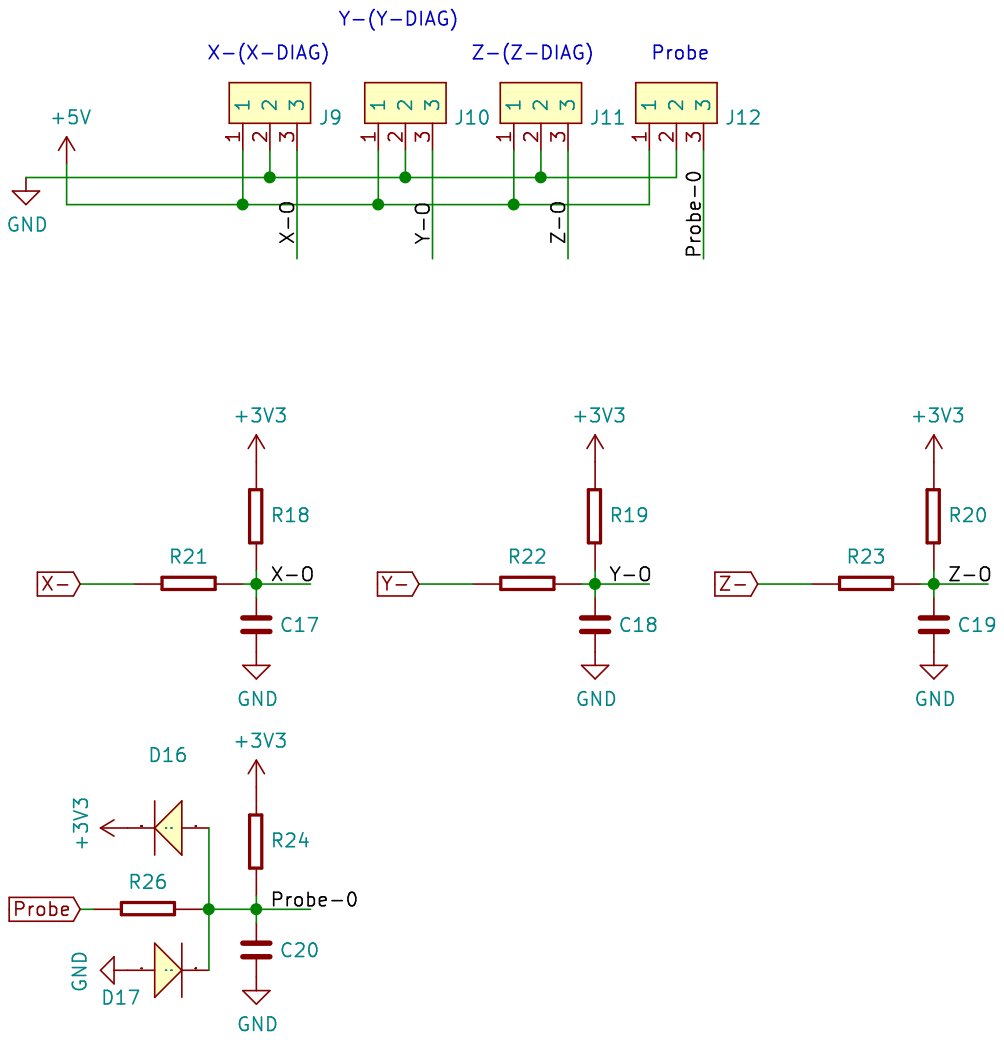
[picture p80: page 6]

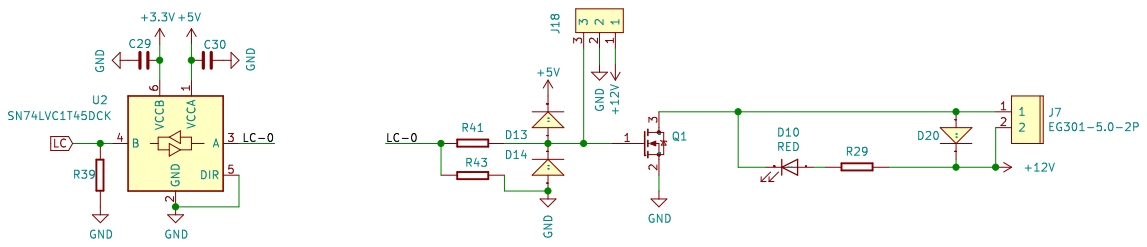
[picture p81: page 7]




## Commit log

2021-09-11 Uploade sch and pin pdf file #5
2021-12-27 Upload the wiring manual of DLC32 V2.X hardware
2024-02-28 update file info
    [MKS LS ESP32新增指令说明-09.xlsx, MKS TS35-R.DXF]
2024-09-12 Delete MKS-ESP32-PRO-main/TFT35-firmware directory
    tft35 firmware mistake
2024-09-12 Delete MKS-ESP32-PRO-main/firmware directory
    outdated firmware
2025-02-05 Add files via upload
    dlc32 max board command
    [ESP32 S1+ESP32 S3新增指令说明-09.xlsx]
2025-02-05 Add files via upload
    update pin.pdf
